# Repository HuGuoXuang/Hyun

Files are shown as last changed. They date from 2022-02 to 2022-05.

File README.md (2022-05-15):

# 轮腿机器人——Hyun

## 问题：
- 硬件的工程文件已经重新上传，之前由于上传文件大于25M导致文件缺失了一些无法正常打开。
- 不建议使用电机自带的磁铁，否则编码器IC读到的噪声会很大。
- 陀螺仪要是焊接到主板上就要修改程序的横滚角和俯仰角。
- 第一次制作不建议在程序里加代码，会影响算法的刷新频率，导致Hyun出现抖动。

## 演示视频
<a href="https://www.bilibili.com/video/BV1Ub4y1s737?spm_id_from=333.999.0.0">
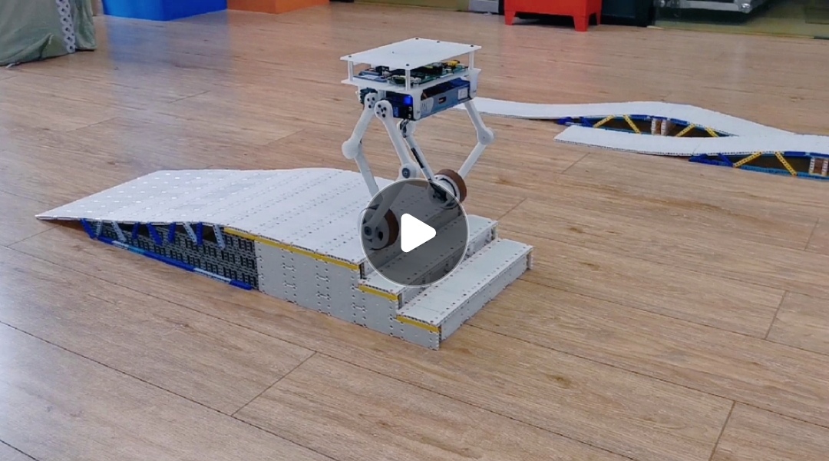
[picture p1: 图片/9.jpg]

</a>

## 装配教程
<a href="https://www.bilibili.com/video/BV1Xt4y1s7Ci?spm_id_from=333.999.0.0">
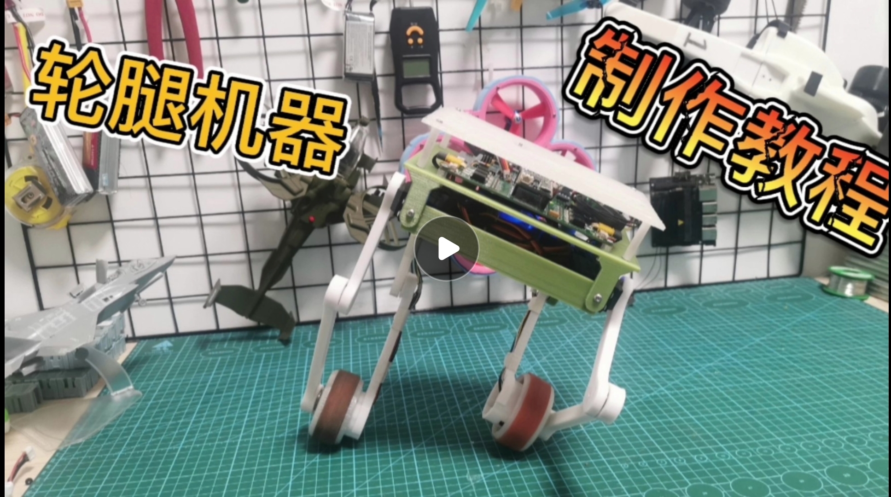
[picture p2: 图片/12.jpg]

</a>

## 搭建开发环境教程
<a href="https://www.bilibili.com/video/BV1z34y1h7pm?spm_id_from=333.999.0.0">
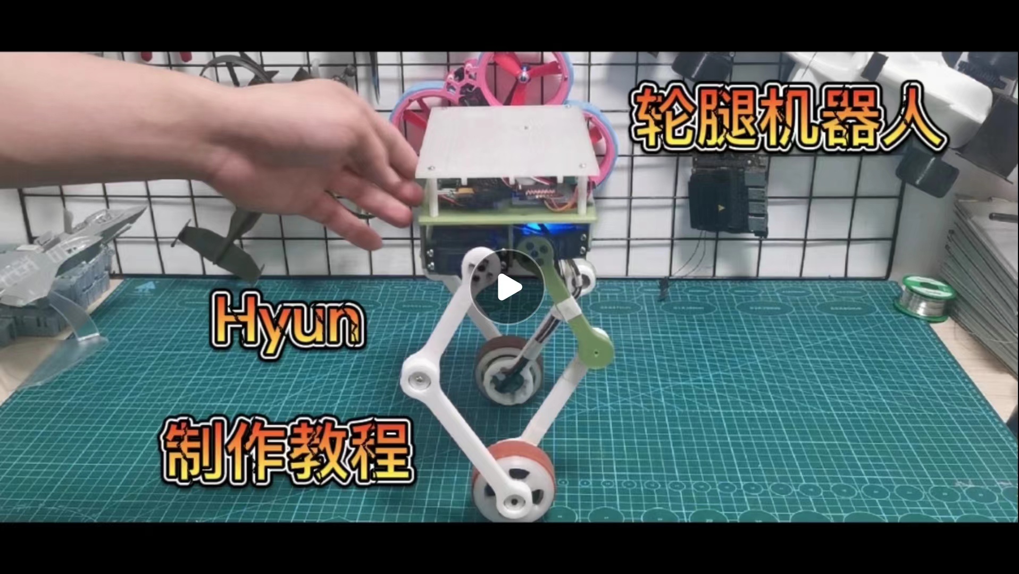
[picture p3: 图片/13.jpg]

</a>

### 1. 主板PCB

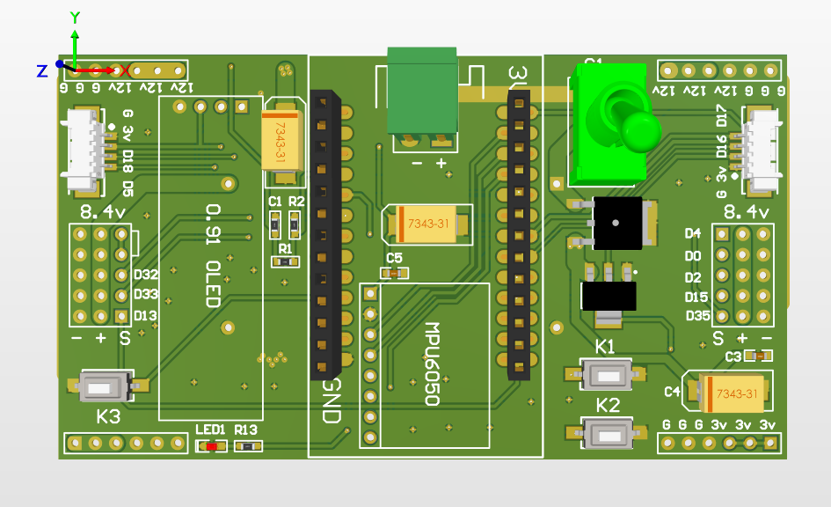
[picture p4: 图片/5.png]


### 2. FOC驱动器PCB

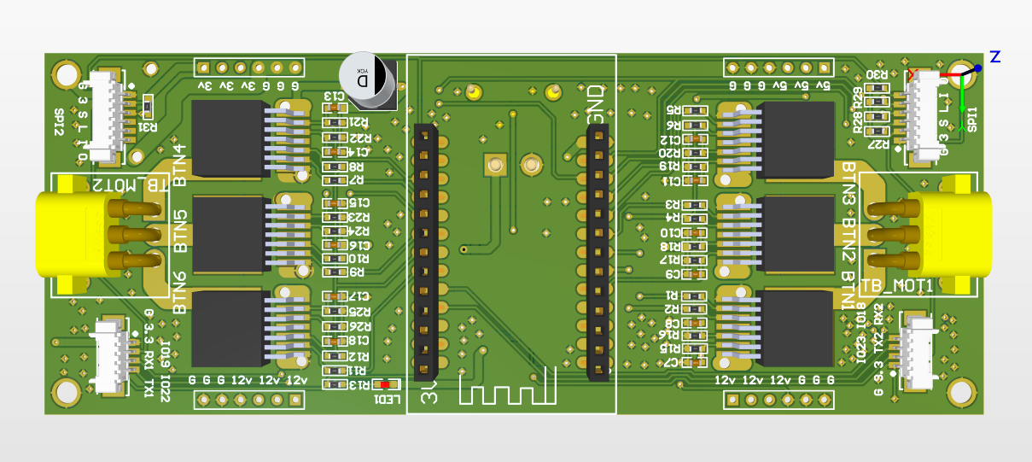
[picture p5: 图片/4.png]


### 3. 磁编码器PCB

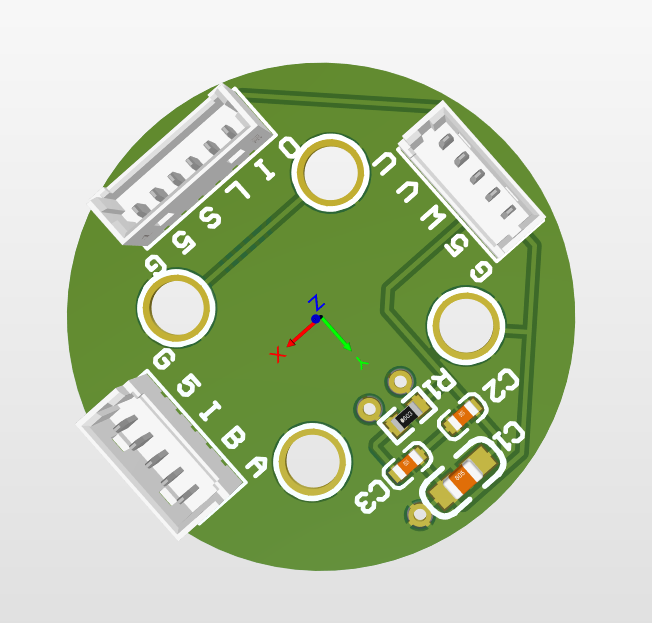
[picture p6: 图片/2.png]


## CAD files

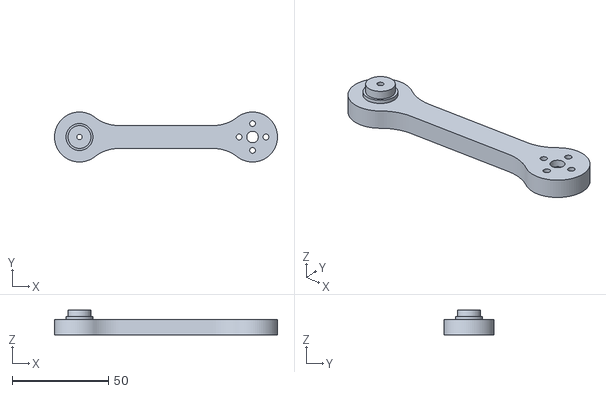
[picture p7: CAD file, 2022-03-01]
3D/stl/5.stl
116.0 x 26.0 x 13.0

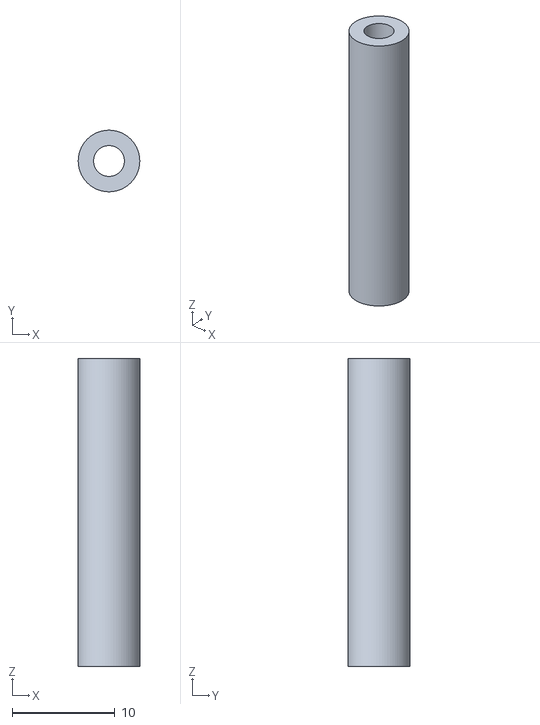
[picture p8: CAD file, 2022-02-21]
3D/stl/11.stl
6.00 x 5.99 x 30.0

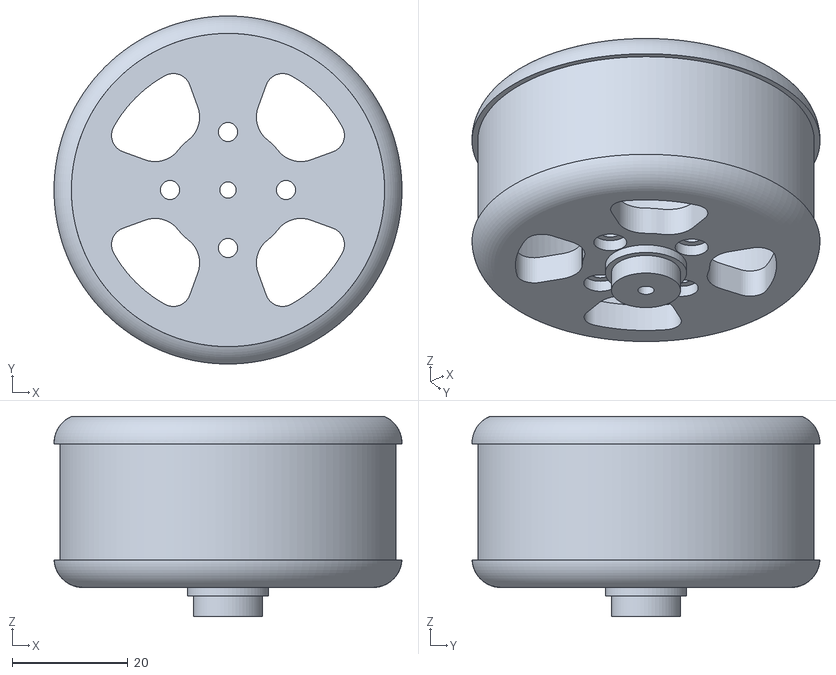
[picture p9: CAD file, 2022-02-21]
3D/stl/2.stl
60.0 x 60.0 x 34.5

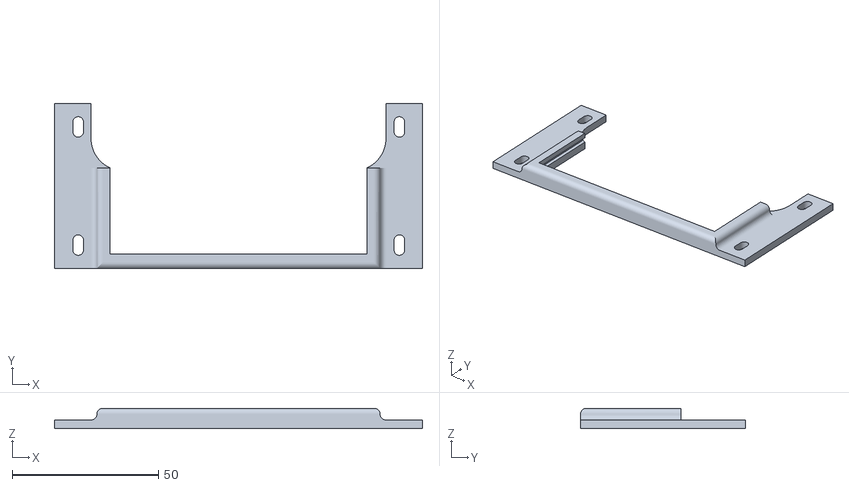
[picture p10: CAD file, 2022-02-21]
3D/stl/9.stl
125.8 x 56.4 x 7.00

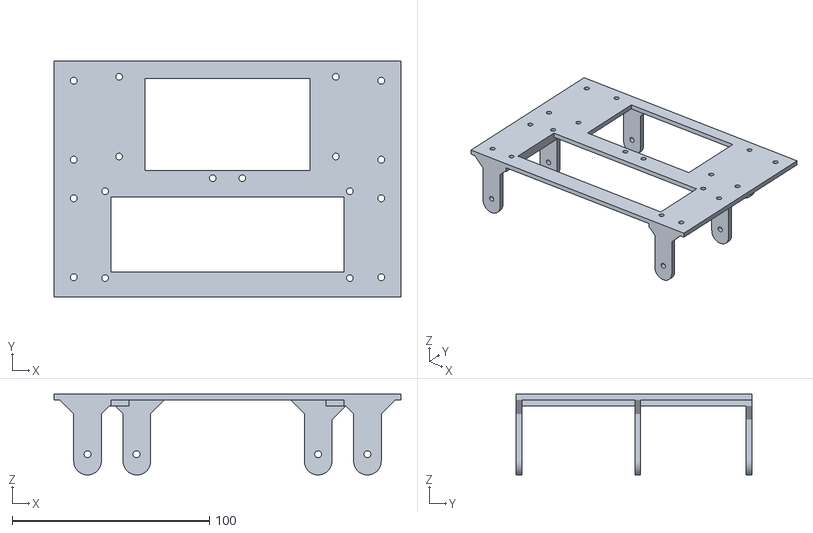
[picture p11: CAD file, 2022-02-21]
3D/stl/7.stl
175.8 x 119.6 x 41.0

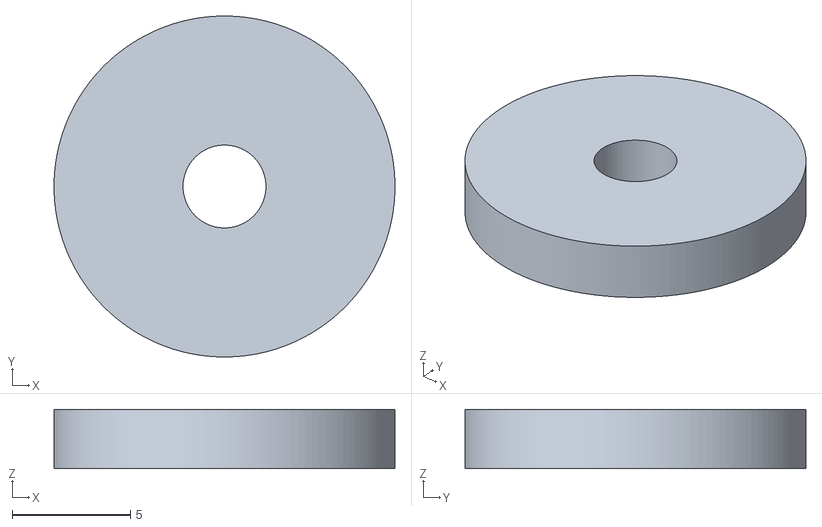
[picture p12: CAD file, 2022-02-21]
3D/stl/14.stl
14.4 x 14.4 x 2.50

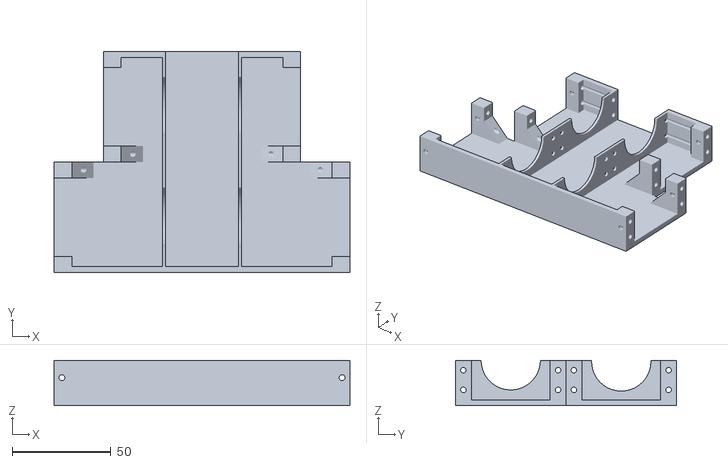
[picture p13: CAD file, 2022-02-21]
3D/stl/6.stl
150.0 x 112.0 x 23.0

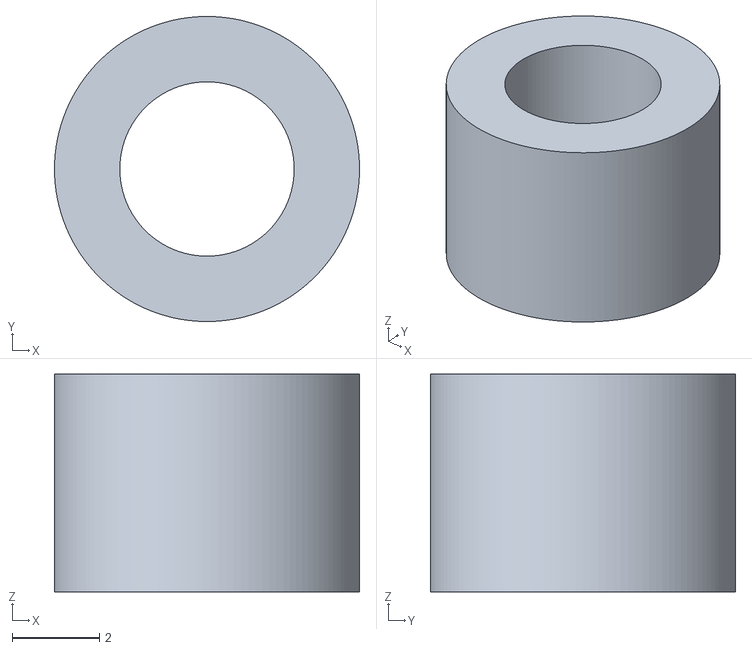
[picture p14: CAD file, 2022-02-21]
3D/stl/13.stl
7.00 x 7.00 x 5.00

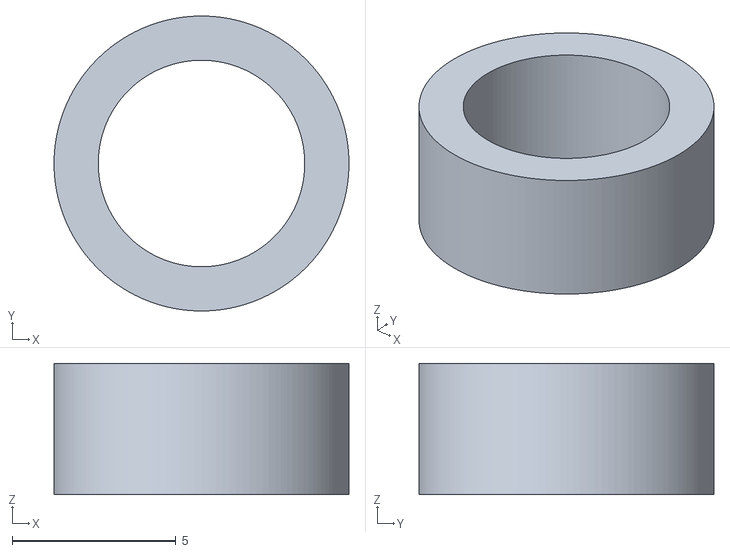
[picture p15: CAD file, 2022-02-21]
3D/stl/12.stl
9.00 x 9.00 x 4.00

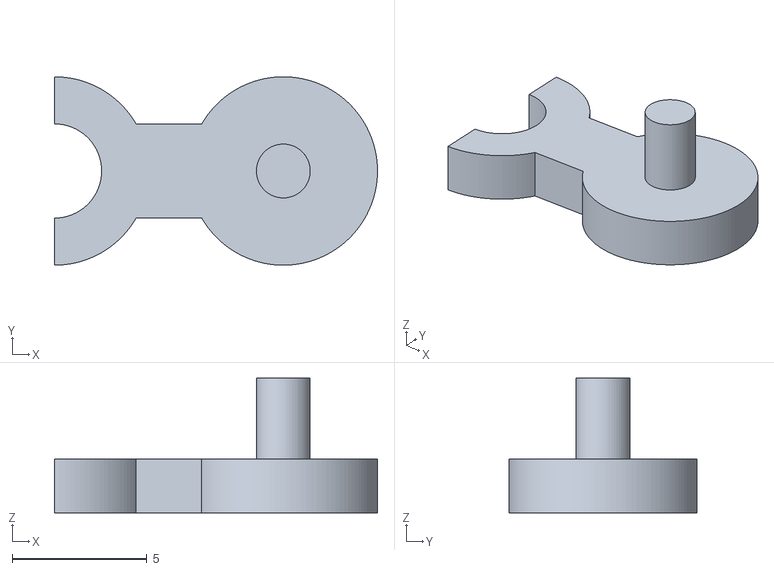
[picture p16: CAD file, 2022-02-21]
3D/stl/10.stl
12.0 x 7.00 x 5.00

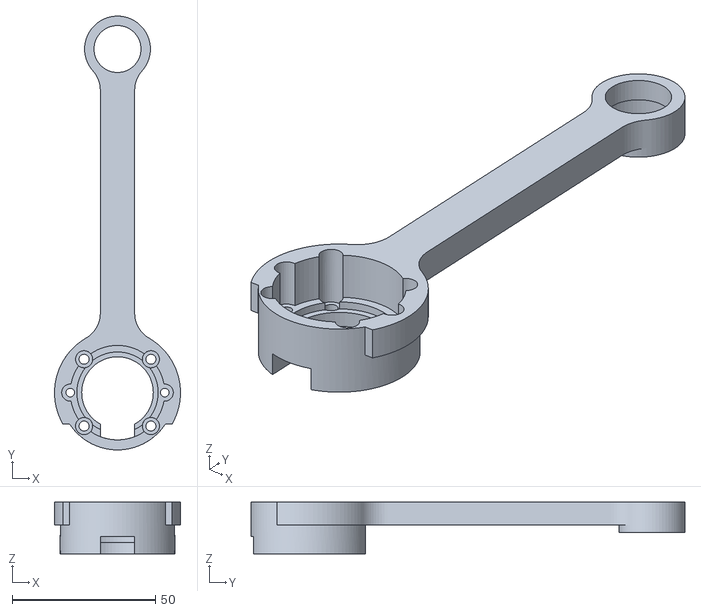
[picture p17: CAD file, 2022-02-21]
3D/stl/1.stl
44.0 x 151.5 x 18.0

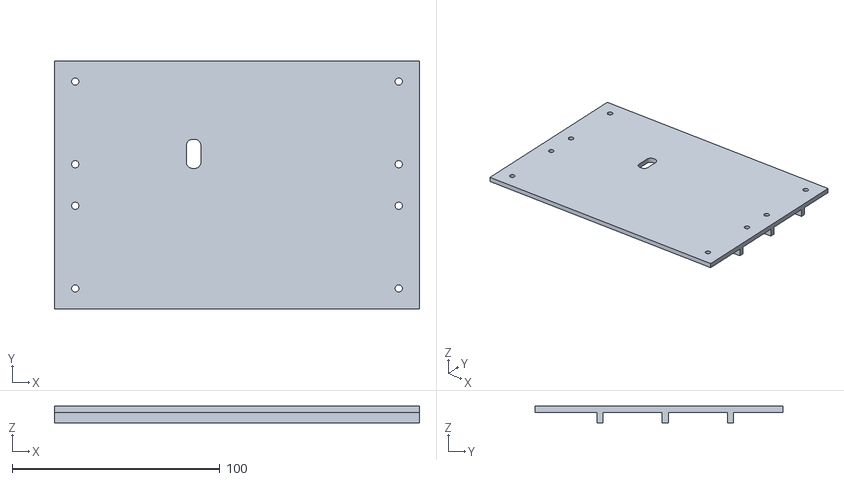
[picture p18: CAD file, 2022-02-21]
3D/stl/8.stl
175.8 x 119.6 x 8.00

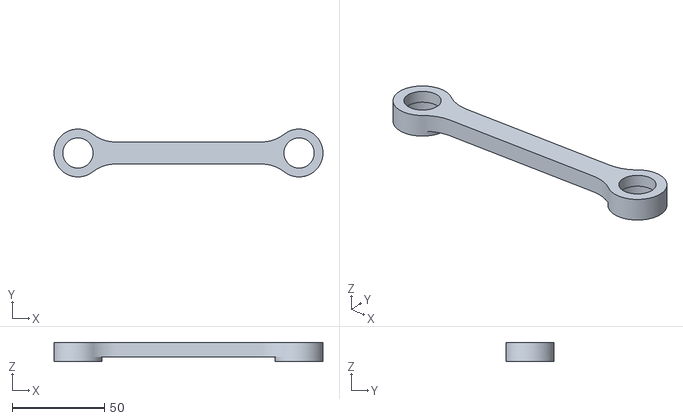
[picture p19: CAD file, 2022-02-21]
3D/stl/3.stl
146.0 x 26.0 x 10.5

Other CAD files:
3D/stl/4.stl

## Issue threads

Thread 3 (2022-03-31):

请教横滚角自动平衡问题

flamebox, 2022-03-31:
请问这版开源代码有实现视频上的横滚角自动平衡吗？我读代码关于这部分不是很理解，不知道具体是哪步实现的。

另外，请问jdbz这个变量具体是什么作用呢，处于这个模式下，似乎是根据ab两边的高度实时调整了速度环和平衡环的pid参数
`Abalance.Kp = -0.00002*sq(ah)+0.0357*ah+1.9519;
  Abalance.Ki = 0.0005*sq(ah)+0.1415*ah+11.045;
  Abalance.Kd = 0;

  Avelocity.Kp = 0.00001*sq(ah)-0.0025*ah+0.2509;
  Avelocity.Ki = 0.00003*sq(ah)-0.0053*ah+0.303;
  Avelocity.Kd = 0;

  Bbalance.Kp = -0.00002*sq(bh)+0.0357*bh+1.9519;
  Bbalance.Ki = 0.0005*sq(bh)+0.1415*bh+11.045;
  Bbalance.Kd = 0;

  Bvelocity.Kp = 0.00001*sq(bh)-0.0025*bh+0.2509;
  Bvelocity.Ki = 0.00003*sq(bh)-0.0053*bh+0.303;
  Bvelocity.Kd = 0;  `
这里的各种系数到底怎么确定的？根据什么理论模型的呢？

最后实时高度的计算AH = 140+ah1+ah2-53.9，这个140和53.9到底是怎么的出来的啊？

我对你这个机器人十分感兴趣，有强烈的愿望想自己学习复现，但本人才疏学浅，不理解的问题比较多，望赐教，谢谢

HuGuoXuang, 2022-04-13:
jdbz 判断轮腿是否摔倒  用来切换摔倒时的PID参数  这份代码就是视频看到效果的源代码  代码都是想到什么就写什么  写得比较乱 没有用到数学模型 理论除了PID就没了   如果你要用搞数学建模 你可以简单的看成两个可以改变摆杆长度的倒立摆 不过要做一些限制 比如倾斜角度是一样

flamebox, 2022-04-13:
>

感谢作者回复。最近也在不断学习，收获颇大。

Closed 2022-05-17.

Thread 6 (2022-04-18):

请问舵机的型号是？或者说选择舵机有什么参考吗？

South-River, 2022-04-18:
如题

HuGuoXuang, 2022-04-19:
资料里的图片有舵机和电机的型号    选择舵机主要考虑机器重量和腿部的加速度是否大于重力加速度g

flamebox, 2022-04-19:
> 资料里的图片有舵机和电机的型号 选择舵机主要考虑机器重量和腿部的加速度是否大于重力加速度g

车子复现出来了，现在发现舵机控制升起时，有点不够力，也不顺畅，是否电流不够？一定要用图片里的航模电池规格吗？一般12v的16850电池组行不行？

HuGuoXuang, 2022-04-20:
检查稳压模块是否有调节到8.4V  稳压模块是给舵机供电的 建议用航模电池 机器的工作电流比较大

HuGuoXuang, 2022-04-20:
> > 资料里的图片有舵机和电机的型号 选择舵机主要考虑机器重量和腿部的加速度是否大于重力加速度g
>
> 车子复现出来了，现在发现舵机控制升起时，有点不够力，也不顺畅，是否电流不够？一定要用图片里的航模电池规格吗？一般12v的18650电池组行不行？

检查文稳压模块的电压是否调节到8.4V  高压舵机供电在8.4V  建议用航模电池 机器的工作电流比较大

Closed 2022-04-20.

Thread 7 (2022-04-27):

这个项目，我按照你给的材料，已经完成了，但是发现几个问题。

deng189, 2022-04-27:
1、FOC驱动器  焊接好后，两个电机工作正常，前后左右旋转都没有问题，但是工作一段时间后，moto2就缺相了，moto1和moto2 对调检测传感器和电机是没有问题的，更换btn8982，也是不行，重新焊接一块新的主板，又正常了。但是问题反复存在。
2、固件刷进去后，舵机工作正常，轮毂电机工作正常，传感器工作正常，遥控器正常，mpu偏移也修正了。发现MPU6050_6Axis_MotionApps_V6_12必须用这个本版的库。最新库MPU6050_6Axis_MotionApps612.h这个有问题，获取的角度值很飘。
3、目前最大问题就是悬空测试，俯仰和横滚对调了，不知道是不是MPU6050_6Axis_MotionApps_V6_12这个库的问题，前倾的时候KalmanX.Angle数值变化，横滚的时候KalmanY.Angle数值变化，我修改了
        int Apwm = (int)(Abalance_pin(asd,(KalmanX.Angle-AngleX_bias))*100)-Tpwm;//总的输出 平衡+前进+转弯
        int Bpwm = (int)(Bbalance_pin(bsd,(KalmanX.Angle-AngleX_bias))*100)+Tpwm;
但是平衡环工作依然有问题，下地后机器人前后抖动太厉害，无法稳定。悬空观察机器人前倾时，轮毂确实向前做功，立正后停止做功。是pid参数的问题，还是我找的MPU6050_6Axis_MotionApps_V6_12这个库有问题。希望作者有空能够回复一下，并提供原始MPU6050_6Axis_MotionApps_V6_12库。非常感谢你的共享。

HuGuoXuang, 2022-04-27:
> 1、FOC驱动器 焊接好后，两个电机工作正常，前后左右旋转都没有问题，但是工作一段时间后，moto2就缺相了，moto1和moto2 对调检测传感器和电机是没有问题的，更换btn8982，也是不行，重新焊接一块新的主板，又正常了。但是问题反复存在。 2、固件刷进去后，舵机工作正常，轮毂电机工作正常，传感器工作正常，遥控器正常，mpu偏移也修正了。发现MPU6050_6Axis_MotionApps_V6_12必须用这个本版的库。最新库MPU6050_6Axis_MotionApps612.h这个有问题，获取的角度值很飘。 3、目前最大问题就是悬空测试，俯仰和横滚对调了，不知道是不是MPU6050_6Axis_MotionApps_V6_12这个库的问题，前倾的时候KalmanX.Angle数值变化，横滚的时候KalmanY.Angle数值变化，我修改了 int Apwm = (int)(Abalance_pin(asd,(KalmanX.Angle-AngleX_bias))*100)-Tpwm;//总的输出 平衡+前进+转弯 int Bpwm = (int)(Bbalance_pin(bsd,(KalmanX.Angle-AngleX_bias))*100)+Tpwm; 但是平衡环工作依然有问题，下地后机器人前后抖动太厉害，无法稳定。悬空观察机器人前倾时，轮毂确实向前做功，立正后停止做功。是pid参数的问题，还是我找的MPU6050_6Axis_MotionApps_V6_12这个库有问题。希望作者有空能够回复一下，并提供原始MPU6050_6Axis_MotionApps_V6_12库。非常感谢你的共享。

厉害居然做到这里了
问题一：moto2就缺相了  有可能是磁铁的大小和安装方式引起的。（我没有用云台电机自带的磁铁）
问题二：MPU6050库建议使用一样版本的 刚开始编程时我是用其它库出现问题才换这个的。
问题三：1.俯仰和横滚对调 其实不是程序对调了  为了方便测试 我把MPU6050模块用线引出来安装  ；
               2.下地后机器人前后抖动太厉害  引起这个的原因应该是 陀螺仪安装的位置不是我调参的那个位子   还有一个原因就是
               电机编码器获取的数据有问题 （是问一造成的） 
  明天会在资料里上传 编码器磁铁和安装的图片    还有陀螺仪安装位置的照片   后面有时间我出一期视频

deng189, 2022-04-27:
好的，期待你的更新，再次感谢你的共享。

flamebox, 2022-04-28:
我这边发现电机抖动是很厉害的，研究下来猜测是编码器芯片离云台电机磁铁那里太远了，所以我修改了3d模型，将距离调整至了1mm以内。
横滚角调整时整机抖动太厉害了，我也不知道是电池输出电流不够导致舵机加速度不足还是pid的问题，买了75c的航模电池，还未到，到时验证一下

deng189, 2022-04-28:
mpu6050，不是接在主控pcb那个位置上，作者通过跳线引到机器人中间甲板上，可以看到甲板位置上面有两个固定mpu6050的螺丝孔。

---- 回复的原邮件 ----
| 发件人 | ***@***.***> |
| 日期 | 2022年04月28日 11:21 |
| 收件人 | ***@***.***> |
| 抄送至 | ***@***.******@***.***> |
| 主题 | Re: [HuGuoXuang/Hyun] 这个项目，我按照你给的材料，已经完成了，但是发现几个问题。 (Issue #7) |

我这边发现电机抖动是很厉害的，研究下来猜测是编码器芯片离云台电机磁铁那里太远了，所以我修改了3d模型，将距离调整至了1mm以内。
横滚角调整时整机抖动太厉害了，我也不知道是电池输出电流不够导致舵机加速度不足还是pid的问题，买了75c的航模电池，还未到，到时验证一下

—
Reply to this email directly, view it on GitHub, or unsubscribe.
You are receiving this because you authored the thread.Message ID: ***@***.***>

flamebox, 2022-04-28:
>

那就是pid问题了，自己调账一下应该就恶可以了，我的6050已经焊在板子上了

deng189, 2022-04-29:
你的直立和行走没问题，那我就确定了，传感器与电机磁铁距离太远确实会导致电机抖动，到时我也改一下，关于舵机电流，确实需要大电流支持，我之前用12v，1.5A充电器带舵机也是会抖动，后面上了作者推荐的航模电池问题解决。两腿自动伸缩正常。

> >
>
> 那就是pid问题了，自己调整一下应该就可以了，我的6050已经焊在板子上了。 不过我现在直立和行走是很稳定的，就是横滚角倾斜时，要求两腿自伸缩调整水平时，舵机动作很抖，我感觉时舵机瞬间电流不够

deng189, 2022-04-29:
> 我这边发现电机抖动是很厉害的，研究下来猜测是编码器芯片离云台电机磁铁那里太远了，所以我修改了3d模型，将距离调整至了1mm以内。 横滚角调整时整机抖动太厉害了，我也不知道是电池输出电流不够导致舵机加速度不足还是pid的问题，买了75c的航模电池，还未到，到时验证一下 另外我修改了主板的pcb，增加了一片max3421e，插usb蓝牙适配器，现在可以用ps4手柄控制了。

esp32 自带蓝牙 我用的这个库 #include <PS4Controller.h> 前面没做遥控器的时候也是用蓝牙ps4手柄控制，但是要改好多代码，后面做了一个萝莉控的遥控器来控制，但是蓝牙存在两个个问题，有的esp32能连得上，有的不行，没找到原因，还有就是代码特别占用esp存储空间。

flamebox, 2022-05-07:
> > 我这边发现电机抖动是很厉害的，研究下来猜测是编码器芯片离云台电机磁铁那里太远了，所以我修改了3d模型，将距离调整至了1mm以内。 横滚角调整时整机抖动太厉害了，我也不知道是电池输出电流不够导致舵机加速度不足还是pid的问题，买了75c的航模电池，还未到，到时验证一下 另外我修改了主板的pcb，增加了一片max3421e，插usb蓝牙适配器，现在可以用ps4手柄控制了。
>
> esp32 自带蓝牙 我用的这个库 #include <PS4Controller.h> 前面没做遥控器的时候也是用蓝牙ps4手柄控制，但是要改好多代码，后面做了一个萝莉控的遥控器来控制，但是蓝牙存在两个个问题，有的esp32能连得上，有的不行，没找到原因，还有就是代码特别占用esp存储空间。

用max3421e+USB Host Library的优点是兼容性好，基本大部分手柄和外设都可以接入，代码简单，就是这个芯片现在太难买

HuGuoXuang, 2022-05-09:
> 我这边发现电机抖动是很厉害的，研究下来猜测是编码器芯片离云台电机磁铁那里太远了，所以我修改了3d模型，将距离调整至了1mm以内。 横滚角调整时整机抖动太厉害了，我也不知道是电池输出电流不够导致舵机加速度不足还是pid的问题，买了75c的航模电池，还未到，到时验证一下 另外我修改了主板的pcb，增加了一片max3421e，插usb蓝牙适配器，现在可以用ps4手柄控制了。

不建议使用电机自带的磁铁 噪声很大  我只用的磁铁已经上传到图片里可以参考 第一次制作不建议在程序上加代码 会影响算法的刷新频率 hyun容易出现抖动无法静止

flamebox, 2022-05-10:
>

我已修改了3d模型，现在使用电机自身磁铁电机也和平稳了。舵机抖动问题改用了75c的航模电池确实改善很多。不过横滚角平衡还是很容易翻车~~~尤其当动作激烈时。另外谢谢提醒主循环添加usb蓝牙读取可能影响pid响应处理，我找时间验证一下。

flamebox, 2022-05-10:
> > 我这边发现电机抖动是很厉害的，研究下来猜测是编码器芯片离云台电机磁铁那里太远了，所以我修改了3d模型，将距离调整至了1mm以内。 横滚角调整时整机抖动太厉害了，我也不知道是电池输出电流不够导致舵机加速度不足还是pid的问题，买了75c的航模电池，还未到，到时验证一下 另外我修改了主板的pcb，增加了一片max3421e，插usb蓝牙适配器，现在可以用ps4手柄控制了。
>
> 不建议使用电机自带的磁铁 噪声很大 我只用的磁铁已经上传到图片里可以参考 第一次制作不建议在程序上加代码 会影响算法的刷新频率 hyun容易出现抖动无法静止

我已修改了3d模型，现在使用电机自身磁铁电机也和平稳了。舵机抖动问题改用了75c的航模电池确实改善很多。不过横滚角平衡还是很容易翻车~~~尤其当动作激烈时。另外谢谢提醒主循环添加usb蓝牙读取可能影响pid响应处理，我找时间验证一下。

deng189, 2022-05-16:
项目终于完工了，所有功能测试ok。

HuGuoXuang, 2022-05-16:
> 项目终于完工了，所有功能测试ok。

可以可以

Closed 2022-05-16.

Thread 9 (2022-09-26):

Mpu6050Int()  has error

L-SY, 2022-09-26:
mpu.setClockSource(MPU6050_CLOCK_PLL_ZGYRO);
mpu.setFullScaleGyroRange(MPU6050_GYRO_FS_2000);
mpu.setFullScaleAccelRange(MPU6050_ACCEL_FS_2);
上面三行的参数都有报错，显示
  未定义标识符 "MPU6050_ACCEL_FS_2"
我下载了electroniccats/MPU6050@^0.6.0的库文件，已经成功添加
但是依旧报错
请问作者是不是用的其它版本的MPU6050的库
能够分享一下吗？十分感谢！！

HuGuoXuang, 2022-09-26:
> mpu.setClockSource（MPU6050_CLOCK_PLL_ZGYRO）; mpu.setFullScaleGyroRange（MPU6050_GYRO_FS_2000）; mpu.setFullScaleAccelRange（MPU6050_ACCEL_FS_2）; 上面三行的参数都有报错，显示 未定义标识符 “MPU6050_ACCEL_FS_2” 我下载了electroniccats/MPU6050@^0.6.0的库文件，已经成功添加 但是依旧报错 请问作者是不是用的其它版本的MPU6050的库 能够分享一下吗？十分感谢！！

我的B站账号里 有搭建环境的视频 你看着操作就行 基本上都能编译通过  这个是ESP32开发板管理器的网站：https://www.arduino.cn/package_esp32_index.json

HuGuoXuang, 2022-09-26:
> mpu.setClockSource（MPU6050_CLOCK_PLL_ZGYRO）; mpu.setFullScaleGyroRange（MPU6050_GYRO_FS_2000）; mpu.setFullScaleAccelRange（MPU6050_ACCEL_FS_2）; 上面三行的参数都有报错，显示 未定义标识符 “MPU6050_ACCEL_FS_2” 我下载了electroniccats/MPU6050@^0.6.0的库文件，已经成功添加 但是依旧报错 请问作者是不是用的其它版本的MPU6050的库 能够分享一下吗？十分感谢！！

按照视频安装陀螺仪的库就行

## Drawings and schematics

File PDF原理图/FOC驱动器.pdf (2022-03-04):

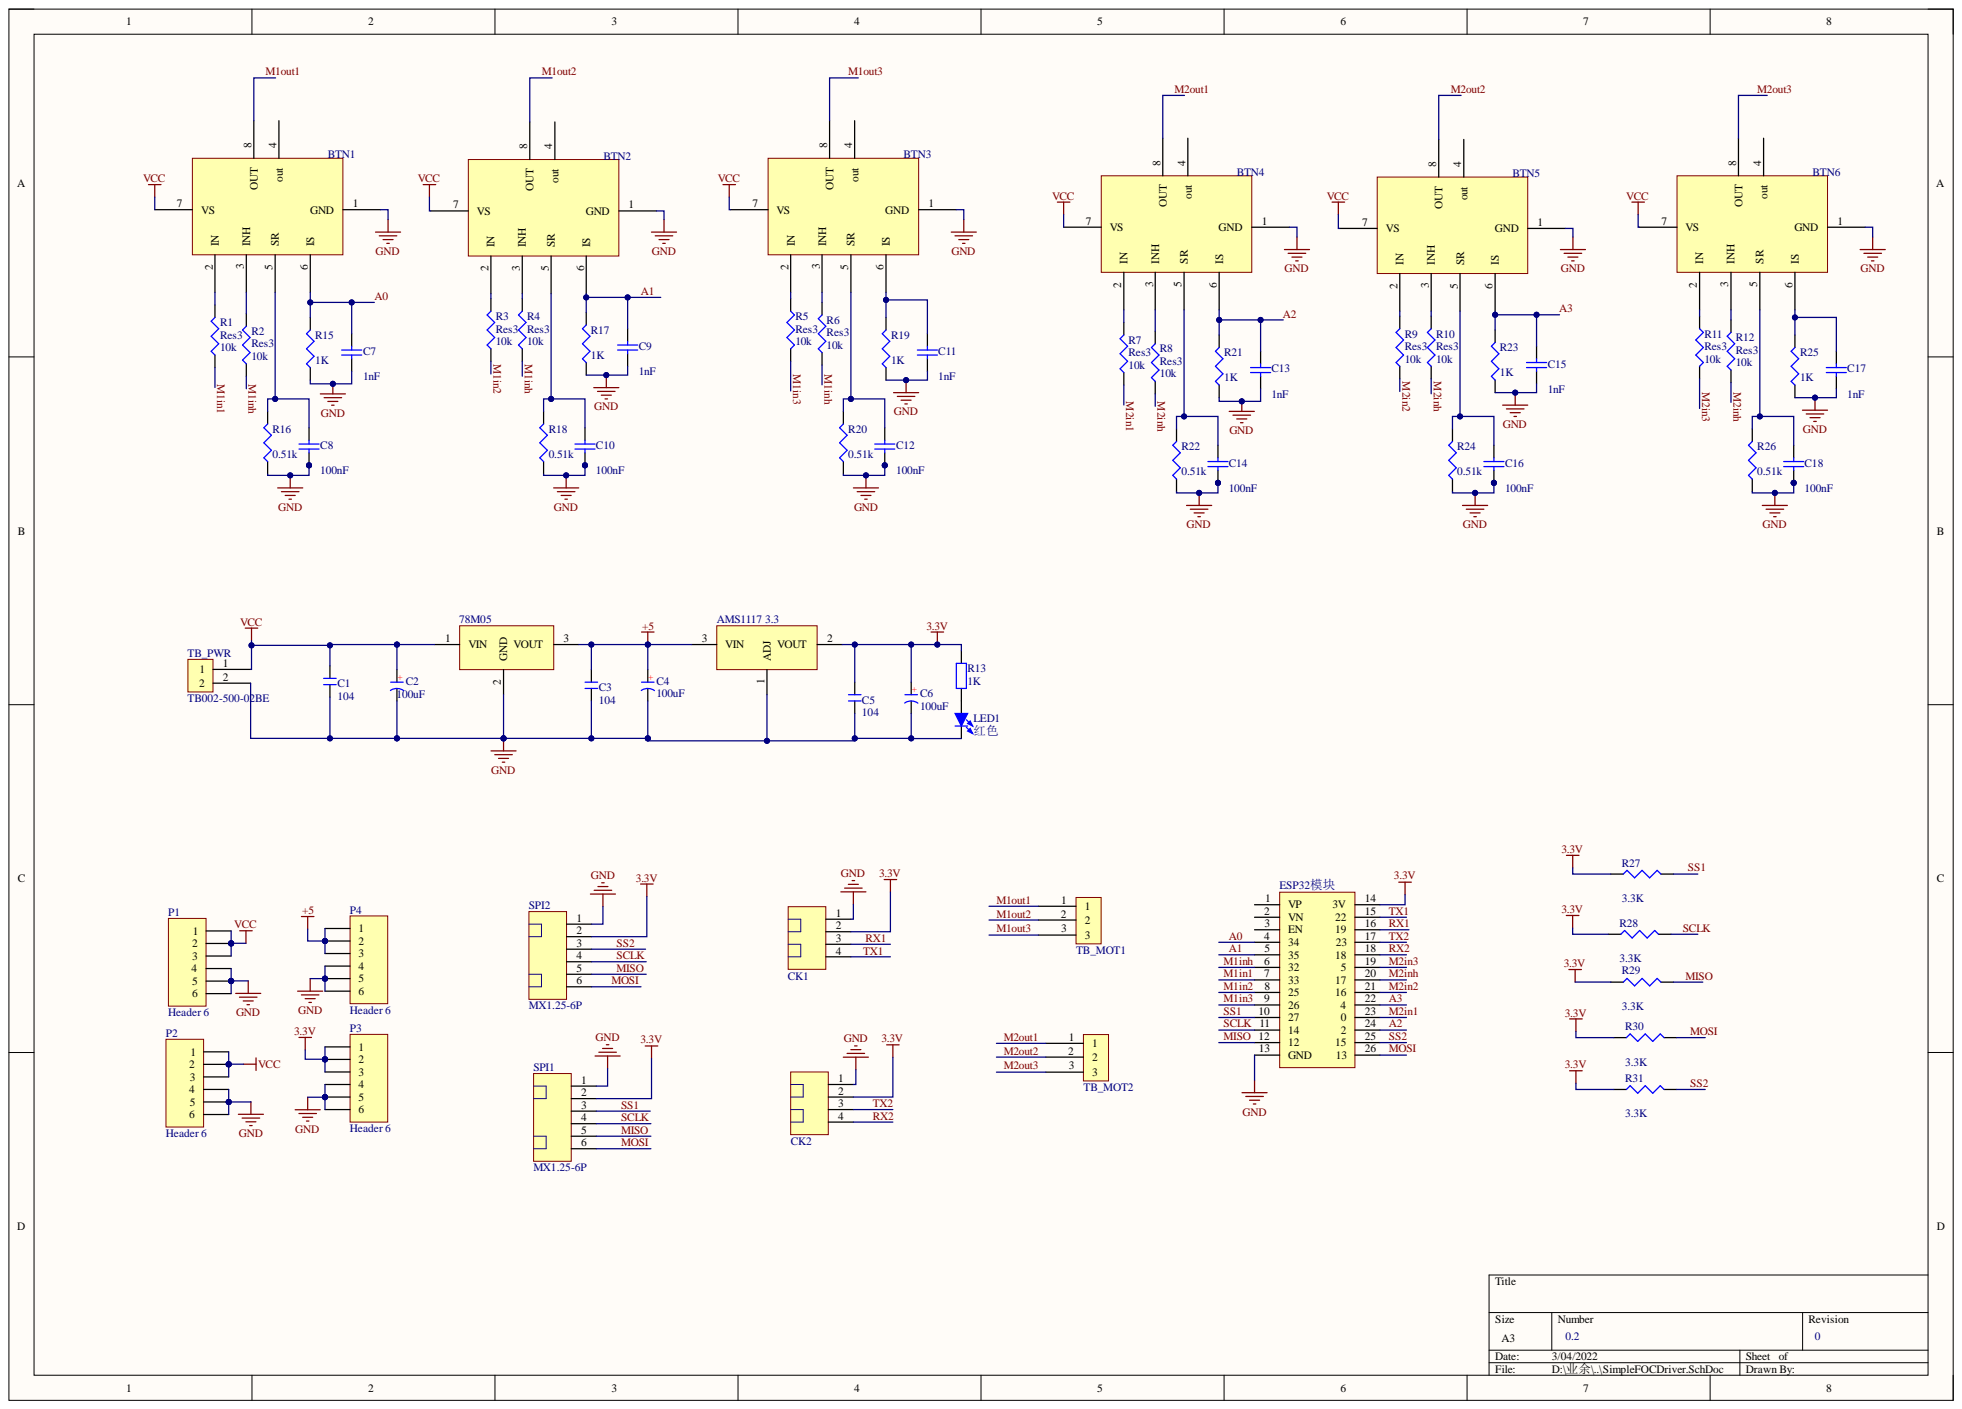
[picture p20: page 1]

Line # | Name | Description | Designator | Quantity | value | Manufacturer 1 | Manufacturer PartNo 1 | Manufacturer Lifecycle 1 | Supplier 1 | Supplier PartNo 1 | Actual Price 1 | Supplier Subtotal 1
| 78M05 | 线性稳压芯片 | 78M05 | 1
| AMS1117 3.3 | 可调线性稳压芯片 | AMS1117 3.3 | 1
| BTN8982 | BTN8982 | BTN1, BTN2, BTN3, BTN4, BTN5, BTN6 | 6 | | | | | RSCompone nts
| 104 | 无极性贴片电容 | C1, C3, C5 | 3
| 100uF | 贴片固态电容 | C2 | 1
| 100uF | 贴片钽电容 | C4, C6 | 2
| Cap Semi | Capacitor (Semiconductor SIM Model) | C7, C9, C11, C13, C15, C17 | 6 1nF
| Cap Semi | Capacitor (Semiconductor SIM Model) | C8, C10, C12, C14, C16, C18 | 6 100nF
| MX1.25-4P | | CK1, CK2 | 2
| ESP32 | | ESP32模块 | 1
| 红色 | 方形LED | LED1 | 1
| Header 6 | Header, 6-Pin | P1, P2, P3, P4 | 4
| Res3 | Resistor | R1, R2, R3, R4, R5, R6, R7, R8, R9, R10, R11, R12 | 12 10k
| 1K | 贴片电阻 | R13 | 1
| Res3 | Resistor | R15, R17, R19, R21, R23, R25 | 6 1K
| Res3 | Resistor | R16, R18, R20, R22, R24, R26 | 6 0.51k
| Res3 | Resistor | R27, R28, R29, R30, R31 | 5 3.3K
| MX1.25-6P | | SPI1, SPI2 | 2
| TB002-500-03BE | | TB_MOT1, TB_MOT2 | 2 | | CUI Devices | TB002-500-03BE | | Mouser | 490-TB002-500-03BE
| TB002-500-02BE | | TB_PWR | 1 | | CUI Devices | TB002-500-02BE | | Mouser | 490-TB002-500-02BE

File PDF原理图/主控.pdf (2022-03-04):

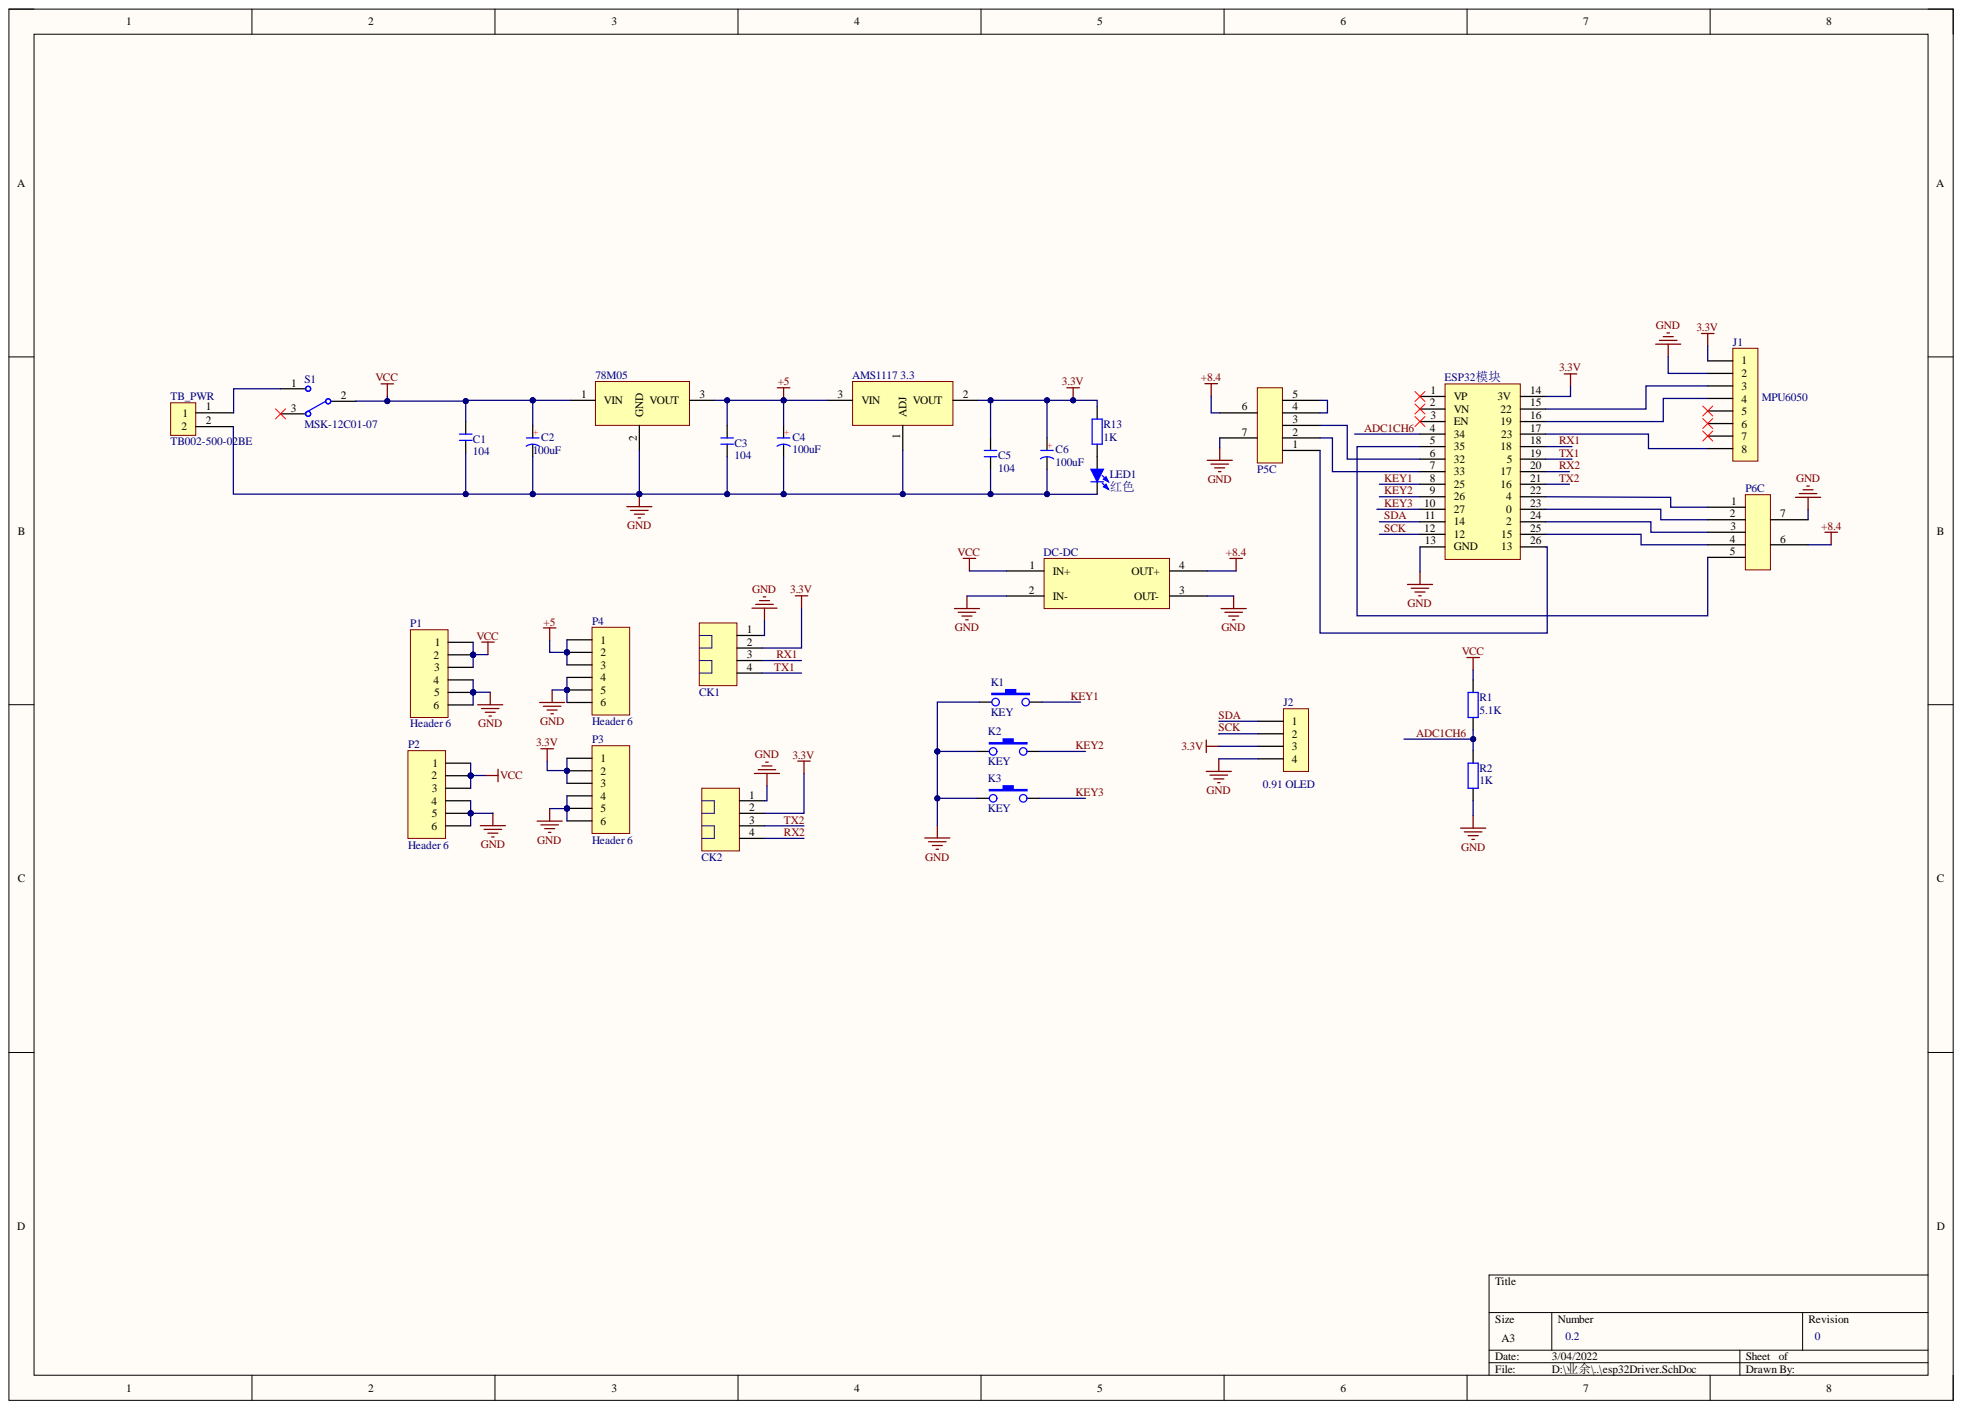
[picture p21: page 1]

5 | | | R X 1
6 | 35 32 17 33 25 26 14 GN 15 13 | T X 1 2 2
7 | | 20 | R X
8 9 1 1 G | | 27 10 12 12 | | T X

25
26

Comment | Description | Designator | Footprint | LibRef | Quantity
78M05 | 线性稳压芯片 | 78M05 | TO252 | 78Mxx | 1
AMS1117 3.3 | 可调线性稳压芯片 | AMS1117 3.3 | SOT223 | LM317 | 1
104 | 无极性贴片电容 | C1 | R 0603_M | C | 1
100uF | 贴片固态电容, 贴片 钽电容 | C2, C4, C6 | C7343-D | C-CT, C-CD | 3
104 | 无极性贴片电容 | C3, C5 | C 0603_M | C | 2
MX1.25-4P | | CK1, CK2 | MX1.25WS-4P | MX1.25-4P | 2
DC-DC | | DC-DC | DC-DC | DC-DC | 1
ESP32 | | ESP32模块 | esp32 | ESP32 | 1
MPU6050 | | J1 | MPU6050 | Pin HDR1X8 | 1
0.91 OLED | | J2 | HDR1X4- OLED | Pin HDR1X4 | 1
KEY | | K1, K2, K3 | SMD-3X6X2.5 | KEY | 3
红色 | 方形LED | LED1 | LED 0603R | LED-F234 | 1
Header 6 | Header, 6-Pin | P1, P2, P3, P4 | HDR1X6 | Header 6 | 4
3*5PIN | | P5, P6 | HDR3X5 | Component_1 | 2
5.1K | 贴片电阻 | R1 | R 0603_M | R | 1
1K | 贴片电阻 | R2, R13 | R 0603_M | R | 2
MSK-12C01-07 | | S1 | MTS-my | MSK-12C01-07 | 1
TB002-500-02BE | | TB_PWR | HT3.96W-2P | TB002-500-02BE | 1

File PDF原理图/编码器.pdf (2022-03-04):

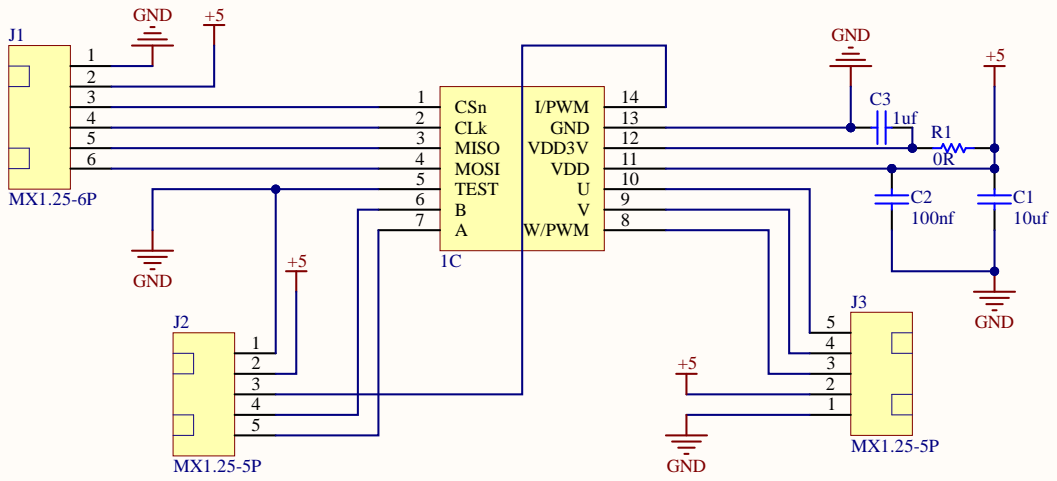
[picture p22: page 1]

2 | | 1 3
3 | | 1 2 1 1
5 | | 1 0

Comment | Description | Designator | Footprint | LibRef | Quantity
AS5147P | | 1 | TSSOP14MAX | AS5147P | 1
Cap | Capacitor | C1 | 0805C | Cap | 1
Cap | Capacitor | C2, C3 | 0603C | Cap | 2
MX1.25-6P | | J1 | MX1.25-6P | MX1.25-6P | 1
MX1.25-5P | | J2, J3 | MX1.25-5P | MX1.25-5P | 2
Res1 | Resistor | R1 | 0603R | Res1 | 1

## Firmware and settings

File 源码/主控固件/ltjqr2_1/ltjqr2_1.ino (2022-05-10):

#include "EEPROM.h"
#include <Arduino.h>
#include <U8g2lib.h>
#include "I2Cdev.h"
#include "MPU6050_6Axis_MotionApps_V6_12.h"
#include "FUTABA_SBUS.h"

#if I2CDEV_IMPLEMENTATION == I2CDEV_ARDUINO_WIRE
#include "Wire.h"
#endif

#define RXD1 16    //串口IO
#define TXD1 17

#define ANALOG_PIN_ch6   34  //电压检测的IO
#define LPF_a 0.7// 滤波系数a(0-1)

#define B1_PWM 2   //舵机IO
#define B2_PWM 0
#define A2_PWM 33
#define A1_PWM 32

#define k1pin 25   //按键IO
#define k2pin 26
#define k3pin 27

#define INTERRUPT_PIN 23  // 陀螺仪外部中断io
MPU6050 mpu;     

U8G2_SSD1306_128X32_UNIVISION_F_HW_I2C u8g2(U8G2_R0,/* reset=*/ U8X8_PIN_NONE , 12 ,14); 

FUTABA_SBUS sBus;
float sbuschx[8] = {0};

int ff = 0;
int ff1 = 0;
int ff2 = 0;

float car_ch1 = 0;     // 旋转
float car_ch2 = 0;     // 油门
float car_ch3 = 800;    // 高度
float car_ch4 = 0;     // 左右
int ch4 = 0;
int car_ch5 = 0;     // 
int car_ch6 = 0;     // 
float car_ch7 = 0;     // 
float car_ch8 = 0;     // 

float Power_Voltage=0;

float abh = 0.1;               
float AbaroAlt = 800;
float BbaroAlt = 800;

float AH = 140;
float BH = 140;

float T_a = 0.1;               
float F_Kionix = 0;

float LPF_value;  //滤波后的值

int show_f = 2;   //显示标志位
int start_f = 0;
int jdbz = 0;
char jdbz_press_time = 0;
char jdbz_press_time1 = 0;
float Ts = 0;     //周期时间
unsigned long Tt; 
unsigned long now_us = 0;
unsigned long velocity_calc_timestamp = 0;

struct{
 
    float Q_angle; 
    float Q_bias; 
    float R_measure; 
    float Angle; 
    float Angle1; 
    float Bias; 
    float Rate; 
    float Rate1;
    float Rate2;

    float p[2][2]; 

}KalmanX,KalmanY,KalmanZ;

/* IMU Data */
bool imuReady = false;  // 
float AngleZ=0,AngleX=0, AngleY=0;              
float AngleX_bias=0, AngleY_bias=0;    
bool dmpReady = false;  
uint8_t mpuIntStatus;  
uint8_t devStatus;      
uint16_t packetSize;    
uint8_t fifoBuffer[64]; 

float Hcm = 0;

int Apwm1 = 0;
int Bpwm1 = 0;
// orientation/motion vars
Quaternion q;           
VectorInt16 aa;         
VectorInt16 gy;         // [x, y, z]            gyro sensor measurements
VectorInt16 aaReal;     // [x, y, z]            gravity-free accel sensor measurements
VectorInt16 aaWorld;    // [x, y, z]            world-frame accel sensor measurements
VectorFloat gravity;    // [x, y, z]            gravity vector
float euler[3];        
float ypr[3];         

volatile bool mpuInterrupt = false;    

boolean  key1,key2,key3;
boolean  s1,s2,s3;
boolean  s1_long_press,s2_long_press,s3_long_press;
char s1_press_time,s2_press_time,s3_press_time,ch5_press_time;
char menu_f = 0;

int freq = 50; // 频率
int resolution0 = 20;   // 分辨率，取值0~20，duty最大取值为2^resolution-1
int channel0 = 0;    // 通道0，共16个通道，0~15
int channel1 = 1;    // 
int channel2 = 2;    // 
int channel3 = 3;    // 


String comdata = "";    //串口接收数据
char terminator = '=';

unsigned char recstatu = 0;//表示是否处于一个正在接收数据包的状态
unsigned char ccnt = 0;//计数
unsigned char packerflag = 0;//是否接收到一个完整的数据包标志
unsigned char rxbuf[7] = {0,0,0,0,0,0,0};//接收数据的缓冲区
unsigned char txbuf[7] = {0,0,0,0,0,0,0};
unsigned char dat = 0;

float B_Angle = 0;//设置机器高度
float A_Angle = 0;

int A1angle_max = 79999;  //设置舵机角度的最大值
int A2angle_max = 77000;
int B1angle_max = 74444;
int B2angle_max = 79999;

int A1angle_mini = 129999; //设置舵机角度的最小值
int A2angle_mini = 28888;
int B1angle_mini = 26000;
int B2angle_mini = 127777;

float Amotor_speed = 0;   //A电机当前速度
float Bmotor_speed = 0;
float Amotor_angle_prev = 0;  //电机上一次的角度
float Bmotor_angle_prev = 0;

uint8_t n_sample = 8;           //滑动加权滤波算法采样个数
float sample_array[8] = {0};    //采样队列

uint8_t n_sample1 = 8;           
float sample_array1[8] = {0};    

uint8_t n_sample2 = 8;           
float sample_array2[8] = {0};    

uint8_t n_sample3 = 8;           
float sample_array3[8] = {0};    

float dead_band = 0;

float newerr = 0;

/////////////////////////////////
 int ix,i1,i2,i3,tx,t0,t1,sta;
 float V_min,V_max,V_mid; 
 long Freq;
 float Vpp;
 float Y[96]; //声明信号值储存数组
 float Buffer[192]; 
 const float L[] PROGMEM = {
0x00,0x00,0x00,0x00,0x00,0x00,0x00,0x00,
0x00,0x00,0x00,0x00,0x00,0x00,0x00,0x00,
0x01,0xC0,0x00,0x00,0x00,0x00,0x00,0x00,
0x00,0x00,0x00,0x00,0x00,0x00,0x00,0x00,
0x01,0xE0,0x00,0x00,0x00,0x00,0x00,0x00,
0x00,0x00,0x00,0x00,0x00,0x00,0x00,0x00,
0x03,0xE0,0x00,0x00,0x00,0x00,0x00,0x00,
0x00,0x00,0x00,0x00,0x00,0x00,0x00,0x00,
0x03,0x70,0x3F,0x87,0xF0,0xC1,0x99,0x83,
0x07,0x80,0x00,0x00,0x00,0x00,0x00,0x00,
0x07,0x30,0x3F,0xC7,0xF8,0xC1,0x99,0xC3,
0x1F,0xE0,0x00,0x00,0x00,0x00,0x00,0x00,
0x06,0x38,0x30,0xC6,0x1C,0xC1,0x99,0xE3,
0x18,0x60,0x00,0x00,0x00,0x00,0x00,0x00,
0x0E,0x18,0x30,0xC6,0x0C,0xC1,0x99,0xF3,
0x30,0x30,0x00,0x00,0x00,0x00,0x00,0x00,
0x0F,0xFC,0x3F,0xC6,0x0C,0xC1,0x99,0xBB,
0x30,0x30,0x00,0x00,0x00,0x00,0x00,0x00,
0x1F,0xFC,0x3F,0x06,0x0C,0xC1,0x99,0x9F,
0x30,0x30,0x00,0x00,0x00,0x00,0x00,0x00,
0x18,0x0E,0x31,0x86,0x1C,0xE3,0x99,0x8F,
0x38,0x70,0x00,0x00,0x00,0x00,0x00,0x00,
0x38,0x07,0x30,0xC7,0xF8,0x7F,0x19,0x87,
0x1F,0xE0,0x00,0x00,0x00,0x00,0x00,0x00,
0x78,0x07,0xB0,0xE7,0xE0,0x3E,0x19,0x87,
0x07,0x80,0x00,0x00,0x00,0x00,0x00,0x00,
0x00,0x00,0x00,0x00,0x00,0x00,0x00,0x00,
0x00,0x00,0x00,0x00,0x00,0x00,0x00,0x00,
0x00,0x00,0x00,0x00,0x00,0x00,0x00,0x00,
0x00,0x00,0x00,0x00,0x00,0x00,0x00,0x00,
0x00,0x00,0x00,0x00,0x00,0x00,0x00,0x00,
0x00,0x00,0x00,0x00,0x00,0x00,0x00,0x00,
0x00,0x00,0x00,0x00,0x00,0x82,0x00,0x10,
0x00,0x00,0x00,0x00,0x80,0x00,0x00,0x00,
0x00,0x00,0x00,0x00,0x04,0x92,0x00,0x08,
0x00,0x00,0x20,0x40,0x80,0x3E,0x78,0x00,
0x00,0x00,0x00,0x00,0x02,0xA4,0x01,0xFF,
0xE0,0x7F,0xC0,0x40,0x80,0x24,0x88,0x00,
0x00,0x00,0x00,0x00,0x02,0xC4,0x02,0x00,
0x40,0x00,0x00,0x08,0x88,0x24,0x88,0x00,
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
}; 
/////////////////////////////////

struct{
    float ActualOut;        //定义实际输出
    float err;              //定义偏差值
    float err_last;         //定义上一个偏差值
    float err_last1;         //定义上一个偏差值
    float Kp,Ki,Kd;         //定义比例、积分、微分系数
    float pidout;           //定义控制执行器的变量
    float integral;         //定义积分值
    float derivative;       //定义微分
    float newerr;
    float newerr1;
    
}Avelocity,Abalance,Bvelocity,Bbalance,Turn,Height;

struct{
  
    float Q_Xk; 

    float R_measure;

    float Xk; 

    float p1; 

}A_speed,B_speed,Zturn;

void dmpDataReady() //陀螺仪外部中断
{
  mpuInterrupt = true;  //陀螺仪中断过标志位
}

float Tfilter(float x)
{
    float TbaroOffset  = x; 
    float Tbaro = T_a * TbaroOffset  + (1.0f - T_a) * F_Kionix;
    F_Kionix = Tbaro;
    return Tbaro;  
}

float Afilter(float x)
{
    float AbaroOffset  = x; 
    float Abaro = abh * AbaroOffset  + (1.0f - abh) * AbaroAlt;
    AbaroAlt = Abaro;
    return Abaro;  
}

float Bfilter(float x)
{
    float BbaroOffset  = x; 
    float Bbaro = abh * BbaroOffset  + (1.0f - abh) * BbaroAlt;
    BbaroAlt = Bbaro;
    return Bbaro;  
}

void sample()  
{   
   Buffer[i3] = Abalance.err;
   i3++;
   if(i3>=192)
   {
      i3 = 0; 
   }
}

void Measure()
{
  V_max=Buffer[0];
  V_min=Buffer[0];      
  for(ix=0;ix<192;ix++)
  { 
    if(Buffer[ix]>V_max) 
    V_max=Buffer[ix];
    if(Buffer[ix]<V_min) 
    V_min=Buffer[ix];
  }
  V_mid=(V_max+V_min)/2;  
  Vpp=V_max-V_mid;
  for(ix=0;ix<97;ix++)
  {
    if(Buffer[ix]<V_mid&&Buffer[ix+1]>=V_mid)  
    {
      i1=ix;
      break;
    }
  }
  for(ix=i1+1;ix<98+i1;ix++)
  {
    if(Buffer[ix]<V_mid&&Buffer[ix+1]>=V_mid)  
    {
      i2=ix;
      break;
    }
  }
  tx=i2-i1;
  if(tx>0)
  Freq=1/(tx*0.01);
  else
  Freq=0;
}

void Transform( )  
{ 
  for(sta=0;sta<96;sta++)
  {
    if(Buffer[sta]<0&&Buffer[sta+2]>0)  
    break;
  } 
  for(ix = 0;ix < 96;ix++)  
  Y[ix] =  Buffer[ix+sta];     
}


void observe()
{
  sample();
  if(i3==0)
  {
    Measure(); 
    Transform();
    for(ix = 0;ix < 96;ix++)  
    {
      Serial.print(Y[ix],3);
      Serial.println("\t"); 
    }     
    Serial.print(Freq,3);
    Serial.print("\t");  
    Serial.print(Vpp,3);
    Serial.println("\t");    
  }
}


void AB_Velocity_filter_init()
{
    A_speed.Q_Xk = 0.01f;
    A_speed.R_measure = 0.001f;
    A_speed.Xk = 0.0f; 
    A_speed.p1 = 0.01f; 

    B_speed.Q_Xk = 0.01f;
    B_speed.R_measure = 0.001f;
    B_speed.Xk = 0.0f; 
    B_speed.p1 = 0.01f;    

    Zturn.Q_Xk = 0.01f;
    Zturn.R_measure = 0.001f;
    Zturn.Xk = 0.0f; 
    Zturn.p1 = 0.01f;     

}


void Kalman_init() { 
    KalmanY.Q_angle = 0.001f;
    KalmanY.Q_bias = 0.003f;
    KalmanY.R_measure = 0.035f;
    KalmanY.Angle = 0.0f; 
    KalmanY.Bias = 0.0f;  
    KalmanY.p[0][0] = 0.0f; 
    KalmanY.p[0][1] = 0.0f;
    KalmanY.p[1][0] = 0.0f;
    KalmanY.p[1][1] = 0.0f;

    KalmanX.Q_angle = 0.001f;
    KalmanX.Q_bias = 0.003f;
    KalmanX.R_measure = 0.035f;
    KalmanX.Angle = 0.0f; 
    KalmanX.Bias = 0.0f;  
    KalmanX.p[0][0] = 0.0f; 
    KalmanX.p[0][1] = 0.0f;
    KalmanX.p[1][0] = 0.0f;
    KalmanX.p[1][1] = 0.0f;

    KalmanZ.Q_angle = 0.001f;
    KalmanZ.Q_bias = 0.003f;
    KalmanZ.R_measure = 0.035f;
    KalmanZ.Angle = 0.0f; 
    KalmanZ.Bias = 0.0f;  
    KalmanZ.p[0][0] = 0.0f; 
    KalmanZ.p[0][1] = 0.0f;
    KalmanZ.p[1][0] = 0.0f;
    KalmanZ.p[1][1] = 0.0f;    
}

void A_Velocity_filter(float NewVelocity )
{
  A_speed.p1 = A_speed.p1+A_speed.Q_Xk;
  float S = A_speed.p1+A_speed.R_measure; 
  float k1 = A_speed.p1/S;
  A_speed.Xk = A_speed.Xk+k1*(NewVelocity-A_speed.Xk);
  A_speed.p1 = (1-k1)*A_speed.p1;
}

void B_Velocity_filter(float NewVelocity )
{

  B_speed.p1 = B_speed.p1+B_speed.Q_Xk;
  
  float S = B_speed.p1+B_speed.R_measure; 
  float k1 = B_speed.p1/S;
  B_speed.Xk = B_speed.Xk+k1*(NewVelocity-B_speed.Xk);
  B_speed.p1 = (1-k1)*B_speed.p1;
}

float Z_turn_filter(float NewVelocity )
{

  Zturn.p1 = Zturn.p1+Zturn.Q_Xk;
  
  float S = Zturn.p1+Zturn.R_measure; 
  float k1 = Zturn.p1/S;
  Zturn.Xk = Zturn.Xk+k1*(NewVelocity-Zturn.Xk);
  Zturn.p1 = (1-k1)*Zturn.p1;

  return Zturn.Xk;
}


void YKalmangGetAngle(float newAngle, float newRate, float dt) {

    KalmanY.Rate = newRate - KalmanY.Bias;
    KalmanY.Angle += dt * KalmanY.Rate;

    KalmanY.p[0][0] += dt * (dt*KalmanY.p[1][1] - KalmanY.p[0][1] - KalmanY.p[1][0] + KalmanY.Q_angle);
    KalmanY.p[0][1] -= dt * KalmanY.p[1][1];
    KalmanY.p[1][0] -= dt * KalmanY.p[1][1];
    KalmanY.p[1][1] += KalmanY.Q_bias * dt;

    float S = KalmanY.p[0][0] + KalmanY.R_measure; // Estimate error

    float K[2]; // Kalman gain - This is a 2x1 vector
    K[0] = KalmanY.p[0][0] / S;
    K[1] = KalmanY.p[1][0] / S;

    float y = newAngle - KalmanY.Angle; // Angle difference

    KalmanY.Angle += K[0] * y;
    KalmanY.Bias += K[1] * y;


    float P00_temp = KalmanY.p[0][0];
    float P01_temp = KalmanY.p[0][1];

    KalmanY.p[0][0] -= K[0] * P00_temp;
    KalmanY.p[0][1] -= K[0] * P01_temp;
    KalmanY.p[1][0] -= K[1] * P00_temp;
    KalmanY.p[1][1] -= K[1] * P01_temp;
}


void XKalmangGetAngle(float newAngle, float newRate, float dt) {

    KalmanX.Rate = newRate - KalmanX.Bias;
    KalmanX.Angle += dt * KalmanX.Rate;

    KalmanX.p[0][0] += dt * (dt*KalmanX.p[1][1] - KalmanX.p[0][1] - KalmanX.p[1][0] + KalmanX.Q_angle);
    KalmanX.p[0][1] -= dt * KalmanX.p[1][1];
    KalmanX.p[1][0] -= dt * KalmanX.p[1][1];
    KalmanX.p[1][1] += KalmanX.Q_bias * dt;

    float S = KalmanX.p[0][0] + KalmanX.R_measure; // Estimate error

    float K[2]; // Kalman gain - This is a 2x1 vector
    K[0] = KalmanX.p[0][0] / S;
    K[1] = KalmanX.p[1][0] / S;

    float y = newAngle - KalmanX.Angle; // Angle difference

    KalmanX.Angle += K[0] * y;
    KalmanX.Bias += K[1] * y;


    float P00_temp = KalmanX.p[0][0];
    float P01_temp = KalmanX.p[0][1];

    KalmanX.p[0][0] -= K[0] * P00_temp;
    KalmanX.p[0][1] -= K[0] * P01_temp;
    KalmanX.p[1][0] -= K[1] * P00_temp;
    KalmanX.p[1][1] -= K[1] * P01_temp;
}

void ZKalmangGetAngle(float newAngle, float newRate, float dt) {

    KalmanZ.Rate = newRate - KalmanZ.Bias;
    KalmanZ.Angle += dt * KalmanZ.Rate;

    KalmanZ.p[0][0] += dt * (dt*KalmanZ.p[1][1] - KalmanZ.p[0][1] - KalmanZ.p[1][0] + KalmanZ.Q_angle);
    KalmanZ.p[0][1] -= dt * KalmanZ.p[1][1];
    KalmanZ.p[1][0] -= dt * KalmanZ.p[1][1];
    KalmanZ.p[1][1] += KalmanZ.Q_bias * dt;

    float S = KalmanZ.p[0][0] + KalmanZ.R_measure; // Estimate error

    float K[2]; // Kalman gain - This is a 2x1 vector
    K[0] = KalmanZ.p[0][0] / S;
    K[1] = KalmanZ.p[1][0] / S;

    float y = newAngle - KalmanZ.Angle; // Angle difference

    KalmanZ.Angle += K[0] * y;
    KalmanZ.Bias += K[1] * y;


    float P00_temp = KalmanZ.p[0][0];
    float P01_temp = KalmanZ.p[0][1];

    KalmanZ.p[0][0] -= K[0] * P00_temp;
    KalmanZ.p[0][1] -= K[0] * P01_temp;
    KalmanZ.p[1][0] -= K[1] * P00_temp;
    KalmanZ.p[1][1] -= K[1] * P01_temp;
}

void pidcs()
{
  Abalance.Kp = 1.3;     
  Abalance.Ki = 5;
  Abalance.Kd = 0; 
  
  Avelocity.Kp = 0;
  Avelocity.Ki = 0;
  Avelocity.Kd = 0; 

  Bbalance.Kp = 1.3;     
  Bbalance.Ki = 5;
  Bbalance.Kd = 0;   

  Bvelocity.Kp = 0;
  Bvelocity.Ki = 0;
  Bvelocity.Kd = 0;     
}

void pid_init()  //pid初始化变量
{
  dead_band=0;   //死去范围

  Height.Kp = 0.2;
  Height.Ki = 0.1;
  Height.Kd = 0;
  Height.err = 0; 
  Height.integral = 0;
  Height.pidout = 0;
  Height.ActualOut = 0; 

  Turn.Kp = 0.5;
  Turn.Ki = 0;
  Turn.err = 0; 
  Turn.integral = 0;
  Turn.pidout = 0;
  Turn.ActualOut = 0; 

  //平衡环PID
  Abalance.ActualOut = 0; 
  Abalance.err = 0;  
  Abalance.err_last = 0;
  Abalance.pidout = 0;
  Abalance.integral = 0;
  Abalance.Kp = 1.3;     
  Abalance.Ki = 5;
  Abalance.Kd = 0; 

  //速度环PID
  Avelocity.ActualOut = 0;
  Avelocity.err = 0;
  Avelocity.err_last = 0;
  Avelocity.pidout = 0;
  Avelocity.integral = 0;
  Avelocity.Kp = 0.3;
  Avelocity.Ki = 0.4;
  Avelocity.Kd = 0; 
  Avelocity.newerr = 0;
  Avelocity.newerr1 = 0;

  //平衡环PID
  Bbalance.ActualOut = 0; 
  Bbalance.err = 0;  
  Bbalance.err_last = 0;
  Bbalance.pidout = 0;
  Bbalance.integral = 0;
  Bbalance.Kp = 1.3;     
  Bbalance.Ki = 5;
  Bbalance.Kd = 0; 

  //速度环PID
  Bvelocity.ActualOut = 0;
  Bvelocity.err = 0;
  Bvelocity.err_last = 0;
  Bvelocity.pidout = 0;
  Bvelocity.integral = 0;
  Bvelocity.Kp = 0.3;
  Bvelocity.Ki = 0.4;
  Bvelocity.Kd = 0; 
  Bvelocity.newerr = 0;
  Bvelocity.newerr1 = 0;  
}


void PID_parameter1(float ah,float bh)
{

  Abalance.Kp = -0.00002*sq(ah)+0.0357*ah+1.9519;     
  Abalance.Ki = 0.0005*sq(ah)+0.1415*ah+11.045;     
  Abalance.Kd = 0; 

  Avelocity.Kp = 0.00001*sq(ah)-0.0025*ah+0.2509;    
  Avelocity.Ki = 0.00003*sq(ah)-0.0053*ah+0.303;     
  Avelocity.Kd = 0;     

  Bbalance.Kp = -0.00002*sq(bh)+0.0357*bh+1.9519;     
  Bbalance.Ki = 0.0005*sq(bh)+0.1415*bh+11.045;     
  Bbalance.Kd = 0; 

  Bvelocity.Kp = 0.00001*sq(bh)-0.0025*bh+0.2509;    
  Bvelocity.Ki = 0.00003*sq(bh)-0.0053*bh+0.303;     
  Bvelocity.Kd = 0;  
  
}


void PID_parameter(float ah,float bh)
{
  Abalance.Kp = 0.00001*sq(ah)+0.0068*ah+0.1028;     
  Abalance.Ki = 0.00002*sq(ah)+0.0396*ah+0.8171;     
  Abalance.Kd = 0; 

  Avelocity.Kp = 0.000002*sq(ah)-0.002*ah+0.539;    
  Avelocity.Ki = -0.002*ah+0.6857;  
  Avelocity.Kd = 0;   

  Bbalance.Kp = 0.00001*sq(ah)+0.0068*ah+0.1028;    
  Bbalance.Ki = 0.00002*sq(ah)+0.0396*ah+0.8171; 
  Bbalance.Kd = 0; 

  Bvelocity.Kp = 0.000002*sq(ah)-0.002*ah+0.539;     
  Bvelocity.Ki = -0.002*ah+0.6857;    
  Bvelocity.Kd = 0;   

  if(Abalance.Kp<1.3)
  Abalance.Kp = 1.3;

  if(Bbalance.Kp<1.3)
  Bbalance.Kp = 1.3;
 
/*
  Bbalance.Kp = Abalance.Kp;     
  Bbalance.Ki = Abalance.Ki;     
  Bbalance.Kd = 0; 

  Bvelocity.Kp = Avelocity.Kp;    
  Bvelocity.Ki = Avelocity.Ki;     
  Bvelocity.Kd = 0; 
 */

}



float Height_pid(float Target,float tilt)
{         
    Height.err =  tilt-Target;

    if(abs(Height.err)<=2)
    {
       Height.err = 0;  
    }

    float p = Height.Kp*(Height.err-Height.err_last);
    float i = Height.Ki*Height.err;
    float d = Height.Kd*(Height.err-2*Height.err_last+Height.err_last1);
      
    Height.pidout = Height.pidout+p+i+d;
   
    Height.err_last = Height.err;
    
    Height.err_last1 = Height.err_last;

    if(Height.pidout>80)
    Height.pidout = 80;  
    else if(Height.pidout<(-80))
    Height.pidout = -80;   
    
    Height.ActualOut = Height.pidout*10;
    
    return Height.ActualOut;
}

float Turn_PID (float Target,float z)
{      
   float zx = T_Sliding_weighted_filter(z);    
   Turn.err = Tfilter((zx-Target));

   //if(abs(Turn.err)<=80)
   //Turn.err=0;

   Turn.pidout=Turn.Kp*Turn.err;         //位置式PID控制器    
   Turn.ActualOut = Turn.pidout*1.0;
   
   //if(Turn.ActualOut>55)
   // Turn.ActualOut = 55;  
   // else if(Turn.ActualOut<(-55))
   //  Turn.ActualOut = -55;             
   return Turn.ActualOut;   
}
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
void loop() 
{
  now_us = micros();
  Ts = (now_us - velocity_calc_timestamp)*1e-6;
  if(Ts <= 0 || Ts > 0.5) Ts = 1e-3; 
  
  if (Ts>=0.01) //if (mpuInterrupt)
  {      
      velocity_calc_timestamp = now_us; 
      RXsbus();
      if(mpuInterrupt)
      {
        if (hasDataIMU()) 
        {
          Mpu6050Read();
        }     
        mpuInterrupt = false;      
      }

      Read_motor_speed(); 
      Hcm =((IMU_Sliding_weighted_filter(aaWorld.z)-8500)/16.4*Ts);
      if(Power_Voltage<=11)
      {
        //start_f = 0;  
        //Serial.print(Power_Voltage);
        //Serial.print(" ");
        //Serial.print("no electricity ");
      }
      
      ff++;
      if(ff>100)
      {
        ff=0;
        //ff1=random(-10000,10000);
        //ff2=random(-90,90);
      }
      else
      {
        ff1=0;
        ff2=0;
      }

      
      if(start_f==1)
      { 
        int Tpwm = (int)Turn_PID (car_ch1,KalmanZ.Rate);//-gy.z/16.4     

        float asd = Avelocity_pin(car_ch2,Amotor_speed,Bmotor_speed);
        float bsd = Bvelocity_pin(car_ch2,Amotor_speed,Bmotor_speed);
        
        int Apwm = (int)(Abalance_pin(asd,(KalmanY.Angle-AngleY_bias))*100)-Tpwm;
        int Bpwm = (int)(Bbalance_pin(bsd,(KalmanY.Angle-AngleY_bias))*100)+Tpwm;   

        if(Apwm>15000)
        Apwm = 15000;

        if(Apwm<(-15000))
        Apwm = -15000;

        if(Bpwm>15000)
        Bpwm = 15000;

        if(Bpwm<(-15000))
        Bpwm = -15000;
 
        int acz = abs(Apwm-Apwm1);
        int bcz = abs(Bpwm-Bpwm1);
        
        //Serial.print(acz);
        //Serial.println("\t");     
        //Serial.println(KalmanY.Angle);
        Set_motor_speed(-Apwm,-Bpwm);
        Apwm1 = Apwm;
        Bpwm1 = Bpwm;
        //observe();
      }
      else 
      {
        Set_motor_speed(0,0);

        Amotor_speed = 0;
        Bmotor_speed = 0;
        
        dead_band=0;   //死去范围
        //平衡环PID
        Abalance.ActualOut = 0; 
        Abalance.err = 0;  
        Abalance.err_last = 0;
        Abalance.pidout = 0;
        Abalance.integral = 0;
        //速度环PID
        Avelocity.ActualOut = 0;
        Avelocity.err = 0;
        Avelocity.err_last = 0;
        Avelocity.pidout = 0;
        Avelocity.integral = 0;
        Avelocity.newerr = 0;
        Avelocity.newerr1 = 0;

        //平衡环PID
        Bbalance.ActualOut = 0; 
        Bbalance.err = 0;  
        Bbalance.err_last = 0;
        Bbalance.pidout = 0;
        Bbalance.integral = 0;
        //速度环PID
        Bvelocity.ActualOut = 0;
        Bvelocity.err = 0;
        Bvelocity.err_last = 0;
        Bvelocity.pidout = 0;
        Bvelocity.integral = 0;
        Bvelocity.newerr = 0;
        Bvelocity.newerr1 = 0;

        float Tpwm = Turn_PID(car_ch1,KalmanZ.Rate1);//-gy.z/16.4     
        
        int Apwm =(int)(Abalance_pin(Avelocity_pin(0,Amotor_speed,Bmotor_speed),(KalmanY.Angle-AngleY_bias))*100);
        int Bpwm =(int)(Bbalance_pin(Bvelocity_pin(0,Amotor_speed,Bmotor_speed),(KalmanY.Angle-AngleY_bias))*100);
      }       
      //mpuInterrupt = false;   
  

    ReadVoltage();
    Keypad_detection();
    ch4 = Bfilter(car_ch4);
    float c3 = Afilter(car_ch3);
  
    if(car_ch5==1)
    {
      ch5_press_time++;
      if(ch5_press_time>50)
      {
        ch5_press_time=0;
      }    
      //A_Angle = 0;
      //B_Angle = 0;    
    }
    if(car_ch5==2)
    {
      ch5_press_time++;
      if(ch5_press_time>50)
      {
        ch5_press_time=0;
      } 
      //A_Angle = 800;
      //B_Angle = 800;        
    }
    
    if(car_ch6==1)
    {
      A_Angle = c3-ch4*10;
      B_Angle = c3+ch4*10;   
    }
    else if((car_ch6==2)&&(c3<=400))
    {
      float Hpwm = Height_pid(ch4,(KalmanX.Angle-AngleX_bias));
      A_Angle = c3+Hpwm;
      B_Angle = c3-Hpwm; 
    }
    
    if(A_Angle>800)A_Angle=800;
    if(A_Angle<0)A_Angle=0;
    
    if(B_Angle>800)B_Angle=800;
    if(B_Angle<0)B_Angle=0;
    
    Set_servo_Angle(A_Angle,B_Angle);
    if(abs(KalmanY.Angle-AngleY_bias)>30)
    {
      jdbz_press_time1++; 
      if(jdbz_press_time1>20)
       {
         jdbz_press_time1 = 0;
         jdbz = 1; 
       } 
    }
  
  
    if(abs(KalmanY.Angle-AngleY_bias)<1)
    {
       jdbz_press_time++;  
       if(jdbz_press_time>20)
       {
         jdbz_press_time = 0;
         jdbz_press_time1 = 0;
         jdbz = 0; 
       }
    }
  
    if(jdbz==1)
    {
      pidcs();
    }
    else
    {
      PID_parameter(AH,BH);    
    }
    //PID_parameter1(map(A_Angle,0,800,0, 80),map(B_Angle,0,800,0, 80));
    Serialcommand(); 
    //delay(8);
  }  
}

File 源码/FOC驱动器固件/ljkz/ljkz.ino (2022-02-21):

#include <SimpleFOC.h>

#define RXD1 18
#define TXD1 23

unsigned long now_us = 0;
unsigned long now_us1 = 0;

unsigned char recstatu = 0;//表示是否处于一个正在接收数据包的状态
unsigned char ccnt = 0;//计数
unsigned char packerflag = 0;//是否接收到一个完整的数据包标志
unsigned char rxbuf[7] = {0,0,0,0,0,0,0};//接收数据的缓冲区
unsigned char txbuf[7] = {0,0,0,0,0,0,0};
unsigned char dat = 0;


float Amotor_speed = 0;   //A电机当前速度
float Bmotor_speed = 0;
float Amotor_angle_prev = 0;  //电机上一次的角度
float Bmotor_angle_prev = 0;
int js = 0;

float setAsd = 0;//设置A电机速度
float setBsd = 0;//设置B电机速度

// MagneticSensorSPI(int cs, float _cpr, int _angle_register)
// config           - SPI config
//  cs              - SPI chip select pin 
MagneticSensorSPI sensor1 = MagneticSensorSPI(AS5147_SPI, 27);
MagneticSensorSPI sensor2 = MagneticSensorSPI(AS5147_SPI, 15);

//MagneticSensorI2C sensor1 = MagneticSensorI2C(AS5600_I2C);
//MagneticSensorI2C sensor2 = MagneticSensorI2C(AS5600_I2C);
//TwoWire I2Cone = TwoWire(0);
//TwoWire I2Ctwo = TwoWire(1);

// these are valid pins (mosi, miso, sclk) for 2nd SPI bus on storm32 board (stm32f107rc)
SPIClass * hspi = NULL;

// BLDC motor & driver instance
BLDCMotor motor = BLDCMotor(11);
BLDCDriver3PWM driver = BLDCDriver3PWM(33, 25, 26, 32);

BLDCMotor motor2 = BLDCMotor(11);
BLDCDriver3PWM driver2 = BLDCDriver3PWM(0, 16, 5, 17);

float target_angle = 0;      // 初始目标角度为0 


void setup() {
  // 编码器设置
  hspi = new SPIClass(HSPI);
  hspi->begin(14, 12, 13);//(sck, miso, mosi)
  //initialise magnetic sensor1 hardware
  sensor1.init(hspi);  
  sensor2.init(hspi);  

  //I2Cone.begin(12, 13, 400000);
  //I2Ctwo.begin(14, 15, 400000);   //SDA1,SCL1
  //sensor1.init(&I2Cone);
  //sensor2.init(&I2Ctwo);
  
  motor.linkSensor(&sensor1);
  motor2.linkSensor(&sensor2);
  // 驱动设置
  driver.pwm_frequency = 100000;
  driver.voltage_power_supply = 12;
  driver.init();
  motor.linkDriver(&driver);

  driver2.pwm_frequency = 100000;
  driver2.voltage_power_supply = 12;
  driver2.init();
  motor2.linkDriver(&driver2);

  // 选择调制方式为SVPWM
// 选择FOC调制类型
// FOCModulationType::SinePWM; （默认）
// FOCModulationType::SpaceVectorPWM;
// FOCModulationType::Trapezoid_120;
// FOCModulationType::Trapezoid_150;
motor.foc_modulation = FOCModulationType::SpaceVectorPWM;
motor2.foc_modulation = FOCModulationType::SpaceVectorPWM;

  // 控制模式为角度模式
  motor.controller = MotionControlType::velocity;
  motor2.controller = MotionControlType::velocity;
  
  ///*

  //motor.phase_resistance = 0.1; // 12.5 Ohms
  //motor.torque_controller = TorqueControlType::voltage;
  //motor.controller = MotionControlType::torque;
  
  //motor2.phase_resistance = 0.1; // 12.5 Ohms
  //motor2.torque_controller = TorqueControlType::voltage;
  //motor2.controller = MotionControlType::torque;
  //*/
  
  // PID参数
  motor.PID_velocity.P = 2;//0.1;
  motor.PID_velocity.I = 55;//4;
  motor.PID_velocity.D = 0.015;//0;
  motor.P_angle.P = 0.5;

  motor2.PID_velocity.P = 2;//0.1;
  motor2.PID_velocity.I = 55;//4;
  motor2.PID_velocity.D = 0.015;//0;
  motor2.P_angle.P = 0.5;
    
  //其他参数
  motor.voltage_limit = 12;    //最大电压
  motor.velocity_limit = 500;   //最大速度，rad/s
  motor.LPF_velocity.Tf = 0.01;  //速度的滤波时间常数

  motor2.voltage_limit = 12;    //最大电压
  motor2.velocity_limit = 500;   //最大速度，rad/s
  motor2.LPF_velocity.Tf = 0.01;  //速度的滤波时间常数
  // 串口设置
  Serial.begin(500000);
  Serial1.begin(500000, SERIAL_8N1, RXD1, TXD1);  

  //初始化
  motor.init(); 
  motor.initFOC();//(5.8794,Direction::CW);

  motor2.init();  
  motor2.initFOC();//(4.4493,Direction::CCW);

  
  Serial.println(F("Motor ready."));
  Serial.println(F("Set the target angle using serial terminal:"));
  _delay(1000);
}

void loop() {  
  now_us = millis();

  motor.loopFOC();
  motor2.loopFOC();
  motor.move(setAsd);
  motor2.move(setBsd);
  
  Read_serial1(); //串口读数据
  if(js>3)
  {
    setAsd = 0;
    setBsd = 0;
  } 
  if((now_us-now_us1)>=10)
  {
    js++;
    //Serial.println((now_us-now_us1));
    float Amotor_angle = sensor1.getAngle();
    float Bmotor_angle = sensor2.getAngle();
    Amotor_speed = (Amotor_angle - Amotor_angle_prev)/0.01;
    Bmotor_speed = (Bmotor_angle - Bmotor_angle_prev)/0.01;
    Amotor_angle_prev = Amotor_angle; 
    Bmotor_angle_prev = Bmotor_angle;    
    
    Read_motor_speed((int)(Amotor_speed*100),(int)(Bmotor_speed*100));
    now_us1 = now_us;
    //Serial.println(Amotor_speed,3);
  } 
  
}

void Read_motor_speed(int MA, int MB)
{   
  if(MA>30000)
  MA = 30000;
  if(MA<(-30000))
  MA = -30000;

  if(MB>30000)
  MB = 30000;
  if(MB<(-30000))
  MB = -30000;
  
  int ta = MA+32767;
  int tb = MB+32767;
  txbuf[0]=111;
  txbuf[1]=66;
  txbuf[2]=ta>>8;
  txbuf[3]=ta&0xff;
  txbuf[4]=tb>>8;
  txbuf[5]=tb&0xff;
  txbuf[6]=crc2(txbuf);
  Serial1.write(txbuf,sizeof(txbuf));
  
}


boolean crc1(unsigned char buffer[])
{
  unsigned int crc_bit1=0;
  unsigned int sum1=0;
  
  for (int j = 2; j <=5; j++)
  {
    sum1 += buffer[j];
  }
  crc_bit1 = sum1 & 0xff;
  if ((unsigned char)crc_bit1 == buffer[6])
    return true;
  else
    return false;
}

unsigned char crc2(unsigned char buffer[])
{
  unsigned int crc_bit1=0;
  unsigned int sum1=0;
  
  for (int j = 2; j <=5; j++)
  {
    sum1 += buffer[j];
  }
  crc_bit1 = sum1 & 0xff;

  return (unsigned char)crc_bit1;
}
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
